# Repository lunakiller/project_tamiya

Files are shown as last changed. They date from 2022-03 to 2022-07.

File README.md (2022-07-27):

# Project TAMIYA

GitHub repository for custom open-source RC car system based on STM32 microcontrollers. The project is built on top of an old Tamiya QD chassis, which was modified. The repository includes both car and transmitter software along with hardware schematics and the Bachelor's thesis with extensive description of the project.

## Features

- long range (350 m+)
- high speed (35 km/h)
- smooth control (~220 Hz control loop)
- 2.4 GHz two-way communication 
- available driving data:
	- battery voltage and current
	- BLDC shell temperature
	- linear acceleration and angular velocity
	- supports logging to microSD card

## Car

- STM32F303CCT6 MCU
- nRF24L01+ PA + LNA module
- RC servo Emax ES3001
- GoolRC 2435 BLDC 4800Kv with 25A ESC
- OLED display and RGB LED
- ACS712 hall current sensor
- DS18B20 temperature sensor
- MPU6050 IMU

## Transmitter

- STM32F303CCT6 MCU
- nRF24L01+ PA + LNA module
- OLED display and RGB LED
- Custom PCB

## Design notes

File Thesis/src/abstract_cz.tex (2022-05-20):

\section*{Abstrakt}
\vspace{0.5cm}

Tato práce se zaměřuje na vývoj auta na dálkové ovládání poháněného STM32 mikrokontroléry. Popisuje stavbu jak auta, tak i vysílačky, představuje použité hardwarové části a jejich využití a~podrobně vysvětluje řídicí software.

Řídicí systém byl od základu vyvinut na starém podvozku Tamiya a tvoří ho na míru vyrobená ovládací deska s moduly a nezbytný řídicí software. Podvozek byl upraven a vybaven výkonnějším BLDC motorem. Aby bylo možné modernizovat vysílačku, byla navržená vlastní deska plošných spojů. Kromě základních funkcí je vůz vybaven různými senzory a moduly s~možností záznamu dat na micro SD kartu. Stav vozu je také nahlašován zpět do vysílačky a~zobrazován na OLED displeji.

Vyvinutý RC systém je v závěru práce otestován v reálných podmínkách. Kromě toho je změřen maximální kontrolovatelný dosah a maximální rychlost.

\vspace{1cm}
\noindent{\bf Klíčová slova:} STM32, RC auto, řídicí software, vestavěný systém, retrofitting

\noindent{\bf Překlad názvu:} Vývoj RC auta řízeného pomocí STM32 mikrokontrolerů

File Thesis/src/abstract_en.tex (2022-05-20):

\section*{Abstract}
\vspace{0.5cm}

This thesis focuses on the development of a radio-controlled car powered by STM32 microcontrollers. It describes the building of both the car and transmitter, presents hardware parts and~their utilization, and explains the control software in detail.

The controlling system was developed from scratch on top of an old Tamiya chassis and consists of a custom-made control board with modules and necessary control software. The~chassis was modified and equipped with more powerful BLDC motor. In order to retrofit the transmitter, a custom PCB was designed. In addition to the essential functions, the car features various sensors and modules with the ability to log the data to the micro SD card. Also, the car status is reported back to the transmitter and visualized on an OLED display.

The developed RC system is tested in real conditions at the end of the thesis. Besides, the~maximum controllable range and top speed are measured.

\vspace{1cm}
\noindent{\bf Keywords:} STM32, RC car, control software, embedded system, retrofitting

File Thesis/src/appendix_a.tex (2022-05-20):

\includepdf[pages=1, angle=90, scale=0.78, offset=0 -45, pagecommand=\appendix{Schematics}]{fig/ProjectTamiya_Car_schematics.pdf}
\newpage
\includepdf[pages=1, angle=90, scale=0.78, offset=0 -20, pagecommand={}]{fig/ProjectTamiya_TX_schematics.pdf}

\newpage
\appendix{Supplementary material}
The attached DVD shares the same file structure as mentioned GitHub repository and is described below. Only the folders have been compressed into zip archives.

\begin{table}[h]
   \renewcommand{\arraystretch}{1.1}
   \centering
%    \caption{ARM Core utilization in STM32 family}
    \label{tab:abbrev}   
    \begin{tabular}{c c}
       \noalign{\hrule height 1.1pt}\noalign{\smallskip}
	   \bfseries File & \bfseries Contents\\[0.2em]
	\noalign{\hrule height 1.1pt}\noalign{\smallskip}  

Software.zip 			& source codes and drivers for both control applications, shared libraries \\
Hardware.zip 			& KiCad schematics and gerber files \\
3D\_printed\_parts.zip	& STL models for 3D printing \\
Logs.zip					& Two example logs in CSV format \\

       \noalign{\smallskip}\noalign{\hrule height 1.1pt}
    \end{tabular}
\end{table}

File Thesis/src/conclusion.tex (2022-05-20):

%!TEX ROOT=main.tex

\part{Conclusion}
\label{chap:conclusion}
The thesis aimed to utilize the STM32 microcontrollers to develop and control an RC car. STM32 families of microcontrollers were summarized, and their architecture and the most commonly used peripherals were briefly described.

The whole system was developed from scratch, aside from the chassis and other plastic parts. It utilizes readily available parts, including an RC servo and BLDC motor with the controller, sensor boards, and modules. These functional blocks were introduced, and their purpose and actual use were explained. Since it is an RC car, meaning 'Radio Controlled', the control transmitter was developed as well.

A custom control board was designed for both platforms. The car's control board is made on a perfboard and consists primarily of modules and connectors. This approach is simple, quick, flexible, and certainly sufficient for the use case. However, space constraints inside the transmitter asked for a custom PCB design that would provide better space utilization. Therefore, the circuit board was designed according to the original, slightly modified to fulfill current needs, and manufactured.

The resulting RC system was to be unconventional in terms of available features. Accordingly, both the transmitter and the car received an OLED display and RGB LED to report the status. In addition, the car is equipped with various sensors. A micro SD card slot is available to record all the data.

After the hardware design, a control software had to be developed. As the software controls real devices in real time, it is primarily interrupt-driven and implemented with an emphasis on speed to guarantee periodic execution of the control loop and thus smooth control of the car. Nevertheless, it is also designed to be user-friendly and encompasses interactive battery voltage and signal strength indicators that should simplify navigation on display along with other icons.

At the end of the thesis, the RC system is tested in real conditions with successful results. Besides the essential RC car functions, all the unconventional functions also proved to work. The control is responsive. The car's top speed is 35km/h, and the maximum controllable range is 375m.

All the schematics, source code, and 3D models are available at a GitHub repository\footnote{\url{https://github.com/lunakiller/project_tamiya}} and on the attached DVD.

Even though the feature is not implemented in the project's current state, microcontroller pins PA11 and PA12 on the car's control board are reserved for the USB peripheral. Therefore, a single-board computer like RaspberryPi running a control software can possibly control the car through the USB, and the chassis can, for example, become a platform for testing autonomy.

The future work can possibly be replacing the commercial ESC controlling the motor with some custom-made solution that would offer a more advanced motor control algorithm. This upgrade would increase the top speed, prolong battery life, and provide the user with more driving data.

Another future step would be replacing the present 6-axis IMU with a 9-axis IMU with an incorporated magnetometer to obtain the precise position in space and utilize those data for control or mapping purposes. One possibility would be to utilize those data to implement 'stability control' to help steer the car in a skid or at high speeds, where the car is tricky to control.

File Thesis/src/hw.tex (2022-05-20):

%!TEX ROOT=main.tex

\part{Hardware}
\label{chap:hw}
%\section{Indroduction}
%\label{sec:hw_intro}

\section{Chassis and transmitter}
\label{sec:hw_base}
\subsection{Background}
The whole project is built on an old entry-level onroad 1/10 chassis from the \textit{Tamiya Quick Drive} series released on Jul 16, 2003 \cite{tamiya}. The RC car was obtained as a childhood gift. It was pre-assembled and came with a 2-channel transmitter communicating at a frequency of \SI{27}{\MHz}. Later the servo broke, and no repair or upgrade parts were available. Since the repair was nearly impossible, but the rest of the chassis was fully functional, it was the perfect choice for a complete rebuild.

The car featured a sealed gearbox, servo, '280' size brushed motor and \SI{9.6}{\V} Ni-Cd battery pack. Due to the age of the product, not much technical information can be found. Figure \ref{fig:tx_old_pcb} shows the old transmitter PCB.
\begin{figure}[ht]
\centering

\caption{Original transmitter PCB}
\label{fig:tx_old_pcb}
\end{figure}

\subsection{Modifications}
\label{sub:hw_mods}
All the electronics were removed, leaving only the plastic chassis. The broken 5-wire servo was replaced with a 'standard' size hobby servo used in most 1/10 RC cars. The old brushed motor was still functional, but it was decided to replace it with a newer and more powerful one. The only constraint was a shaft size, as the old pinion had to be transferred to the new motor to maintain functionality. Therefore a '2435' size BLDC motor with a \SI{25}{\A} ESC (Electronic Speed Controller) was selected. More information about the servo and BLDC is in sections \ref{sec:hw_servo} and \ref{sec:hw_bldc}. Furthermore, the plastic bearings were replaced by metal ball bearings.

A 2-cell LiPo battery with a capacity of \SI{2200}{\milli\A\hour} was chosen to supply power to the electronics. According to the product specification, this battery should withstand 35C of continuous current~\cite{lipo_car}. The term '35C' means '35 times the battery capacity'. For this particular battery, that means ${35 \cdot \SI{2.2}{\A} = \SI{77}{\A}}$ of current, which is more than sufficient.

The transmitter underwent a similar procedure. The original circuit board and the antenna were also removed, retaining only trigger potentiometers and plastic parts. Potentiometers used for throttle and steering trimming were replaced with rotary encoders. Again, the power supply is a 2-cell LiPo battery with a lower capacity of only \SI{900}{\milli\A\hour} and 25C of continuous current \cite{lipo_tx}.

\section{Servo}
\label{sec:hw_servo}
A servomotor, or servo for short, is an actuator used for precise output shaft positioning. It consists of a motor with position feedback and a control board. RC servos are controlled using a 50Hz PWM signal. The output angle is linearly dependent on a pulse width between \SI{1}{\ms} and \SI{2}{\ms}. The diagram in figure \ref{fig:servo_control} illustrates typical timing.
\begin{figure}[ht]
\centering

\caption{Servomotor timing diagram \cite{servo_control}}
\label{fig:servo_control}
\end{figure}

The servo used in the car is \textit{EMAX} ES3001. It has plastic gears and operating voltage between \SI{4.8}{\V} to \SI{6.0}{\V}. Speed and torque depend on the supply voltage. According to the product specifications \cite{emax}, the servo can achieve an operating speed of $0.17\, \text{s}/60^\circ$ and torque of \SI[inter-unit-product =\ensuremath{\cdot}]{3.2}{\kg\cm} with the \SI{4.8}{\V} supply voltage. From the operating speed we can calculate angular velocity: 
\begin{equation}
\omega = \frac{d \theta}{d t} = \frac{\frac{\pi}{3}}{0.17} \doteq 6.156\ \unit{\radian\per\second}\ ,
\end{equation}
where $\frac{\pi}{3}$ is $60^\circ$ converted to radians.
Since the servo supply voltage is \SI{5}{\V}, both speed and torque values should be slightly higher.

\section{Motor and ESC}
\label{sec:hw_bldc}
As mentioned in section \ref{sub:hw_mods}, the biggest BLDC with a shaft diameter of \SI{2}{\mm} was selected to replace the old brushed one. The motor was supplied in a set including a \SI{25}{\A} ESC. The type is \textit{GoolRC} 2435 \SI{4800}{\Kv}\footnote{\unit{Kv} refers to rpm/V with no load attached to the motor shaft.} BLDC; available information about the motor is in table \ref{tab:BLDC_spec} and about ESC in table \ref{tab:ESC_spec}.
\begin{table}[h]
   %\renewcommand{\arraystretch}{1.1}
   \tabcolsep 18pt
   \centering
    \caption{BLDC specifications}\label{tab:BLDC_spec}   
    \begin{tabular}{l r}
       \noalign{\hrule height 1.1pt}\noalign{\smallskip}	   
	Power			& 300\unit{\W}\\
	Max. voltage   	& 12.6\unit{\V}\\
	Max. current   	& 24\unit{\A}\\
	Rotor poles	   	& 4 \\
	\unit{\Kv} rating	  	& 4800 \\
	Length			& 24\unit{\mm} \\
	Diameter			& 35\unit{\mm} \\
	Shaft diameter	& 2\unit{\mm} \\
       \noalign{\smallskip}\noalign{\hrule height 1.1pt}
    \end{tabular}
\end{table} 
\begin{table}[h]
   %\renewcommand{\arraystretch}{1.1}
   \tabcolsep 12pt
   \centering
    \caption{ESC specifications}\label{tab:ESC_spec} 
    \begin{tabular}{l r}
       \noalign{\hrule height 1.1pt}\noalign{\smallskip}
	Continuous current		& 25\unit{\A}\\
	Instantaneous current   	& 50\unit{\A}\\
	BEC type				   	& 5\unit{\V}, 2\unit{\A}\\
	Battery				   	& 2-3 Cell LiPo \\
       \noalign{\smallskip}\noalign{\hrule height 1.1pt}
    \end{tabular}
\end{table} 

Originally the brass pinion was press-fitted to the motor; however, the shaft began to slip inside the pinion. Therefore it was soldered to the shaft with the help of solder paste and a hot-air station.

Since the BLDC motor is directly connected to the ESC and the control board communicates only with the ESC, the BLDC is considered a black box.

RC ESCs are controlled the same way as RC servos; thus, the same timing diagram in figure \ref{fig:servo_control} applies. The only difference is the resulting motion. Pulse width with a duration of \SI{2}{\ms} equals full forward acceleration, pulse width with a duration of \SI{1.5}{\ms} equals neutral, and pulse width with a~duration of \SI{1}{\ms} equals full brake/reverse.

Whether the brake or reverse is activated depends on the actual motion of the motor. If the car is going forward (meaning the motor rotates forward) and the pulse width becomes lower than \SI{1.5}{\ms}, first, the brake is activated. The car must be almost static to start reversing; otherwise, the ESC will stay in brake mode. If the car is static or is already reversing, a pulse width lower than \SI{1.5}{\ms} activates reverse mode.

\section{Control board}
\label{sec:hw_control}
Prototyping was mainly done on the breadboard using the \textit{RobotDyn's} BlackPill development board featuring STM32F303CCT6 microcontroller \cite{black_pill}. The board uses a similar size and form factor as the popular BluePill board equipped with STM32F103C8T6 \cite{blue_pill}. Both these boards were readily available.
    \begin{figure}[h]
    \centering
    \begin{subfigure}{0.4\textwidth}
    \centering
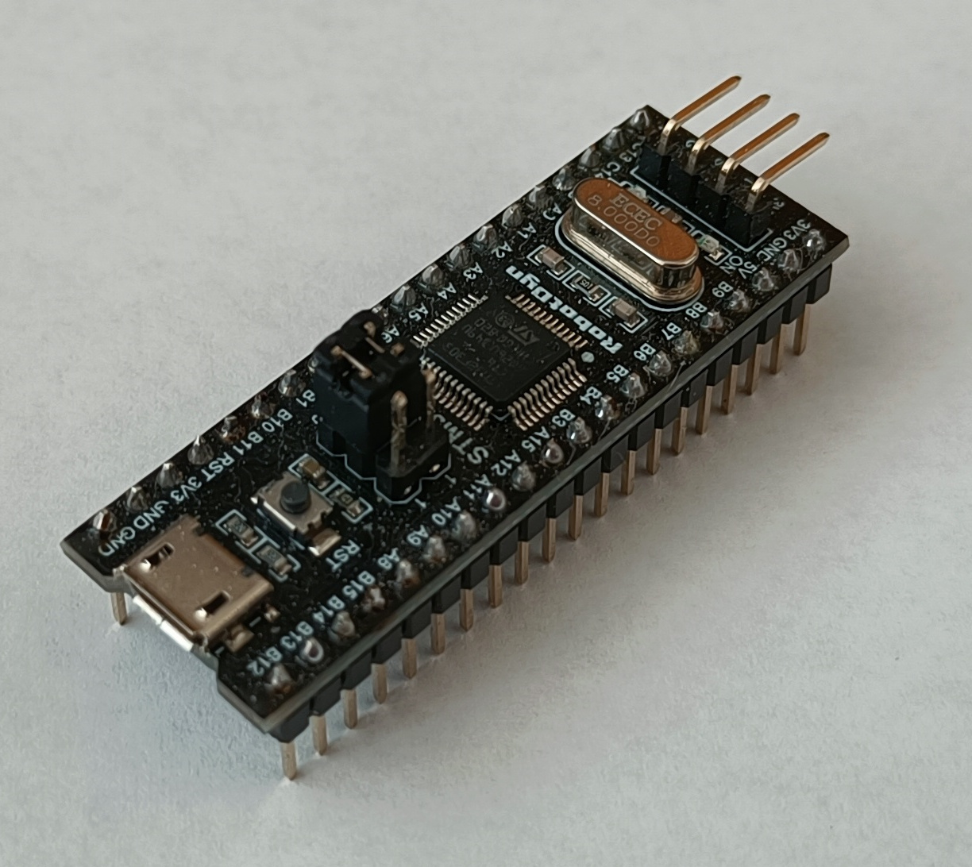
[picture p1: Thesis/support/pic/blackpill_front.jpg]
        
		\caption{front side}
    \end{subfigure}%
    \hspace{1cm}
    \begin{subfigure}{0.4\textwidth}
    \centering
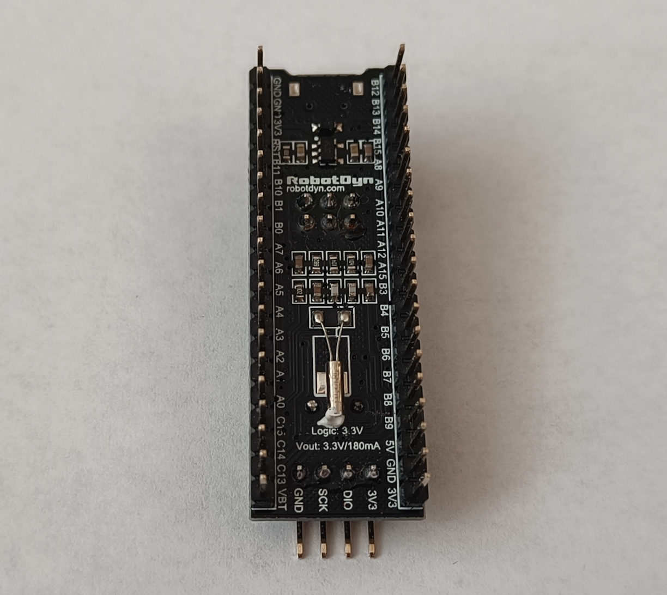
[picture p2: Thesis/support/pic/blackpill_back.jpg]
		
		\caption{back side}
    \end{subfigure}
	\caption{RobotDyn BlackPill development board}
    \label{fig:black_pill}
    \end{figure}

BlackPill was selected for its better processor based on an ARM M4 core with FPU, larger memories, and more advanced peripherals. Thus, it is more suitable for processing data from more sensors, especially when using floating point arithmetics. The board is shown in figure \ref{fig:black_pill}.

%\begin{figure}[t]
%\centering
%\includegraphics[width=0.5\linewidth]{fig/placeholder.jpg}
%\caption{*PLACEHOLDER* RobotDyn BlackPill development board}
%
%\end{figure}

\section{Communication}
\label{sec:hw_comm}
The project uses wireless modules equipped with nRF24L01+ transceiver chip from \textit{Nordic Semiconductor}, a power amplifier, a low-noise amplifier, and an external antenna. The chip operates in the worldwide \SI{2.4}{\GHz} ISM band and communicates with the MCU using the SPI bus. Configurable parameters include channel, data rate, and output power. These modules fit all the requirements, and in addition, they are cheap and readily available.

According to the product specification \cite{nrf_pa_lna}, the range should be more than \SI{800}{\m} line-of-sight. Thanks to the \textit{Enhanced ShockBurst protocol} and its Auto Acknowledgement function \cite{nrf_datasheet}, attaching a small payload to the ACK packet is possible. This feature is advantageously used to report car status back to the transmitter.
\begin{figure}[h]
\centering
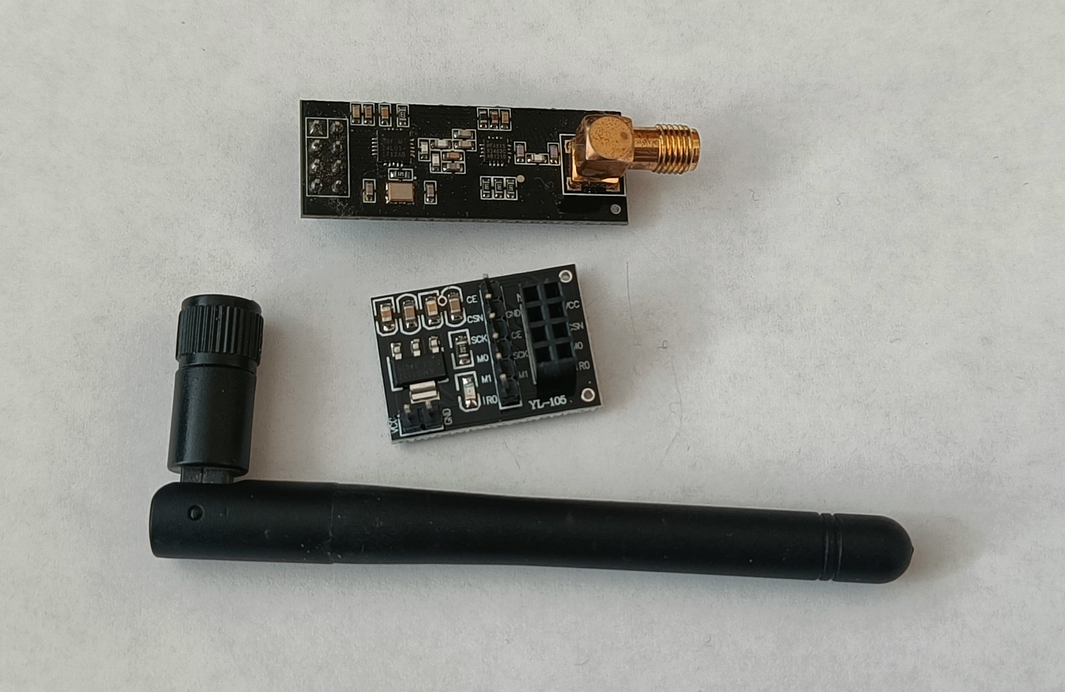
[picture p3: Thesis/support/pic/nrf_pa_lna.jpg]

\caption{Unmodified nRF24 module with adapter}
\label{fig:unmod_nrf}
\end{figure}

An additional adapter board is utilized to supply voltage to the nRF24 module. It has the same pinout and includes a voltage regulator with all needed external components. The Adapter board is powered with \SI{5}{\V}, which are then regulated to \SI{3.3}{\V}. This setup ensures a stable power supply for the nRF24 module.

As the adapter board is only equipped with a pin socket for connection, which is unsuitable for use in vibration generating environments, it was removed. The nRF24 module was instead soldered directly to the adapter, as were the wires. The entire communication module is thus more robust and takes up less space. Figure \ref{fig:unmod_nrf} shows the unmodified communication module with the adapter board.

\section{Sensors}
\label{hw_sensors}
In addition to measuring the voltage, which is necessary for battery monitoring and is realized using a voltage divider, the car also measures current and BLDC case temperature. It is also equipped with 6-axis IMU. In the project's present state, data from sensors are mainly informative and are not used for control purposes.

The transmitter does not use any particular sensor; only battery voltage is measured via the voltage divider.

\subsection{Current}	
The current is measured using a module with a \SI{30}{\A} version of an ACS712 chip from \textit{Allegro MicroSystems}. It is a small linear current sensor based on the Hall effect. Current flowing through the sensor's copper terminals generates a magnetic field, which is then sensed by the integrated Hall-effect circuit. The sensor module is in figure \ref{fig:acs712}.
\begin{figure}[h]
\centering
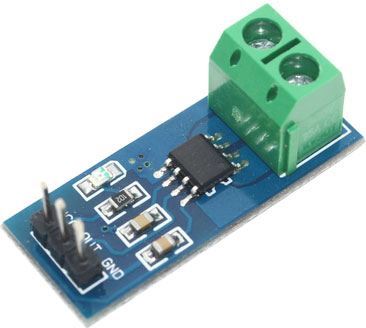
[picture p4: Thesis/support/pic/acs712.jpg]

\caption{ACS712 current sensor \cite{acs_pic}}
\label{fig:acs712}
\end{figure}

The output of the sensor is a voltage proportional to the flowing current. If no current is flowing, the sensor output is the supply voltage divided by two. If a positive current flows, the output voltage increases, whereas the output voltage decreases if the current is negative.

Current sense terminals are electrically isolated from the rest of the sensor; therefore, it is possible to measure high voltages without external electrical isolation. The sensor is capable of measuring both AC and DC current with a stated total output error of $1.5\%$ \cite{acs_datasheet}.

\subsection{Temperature}
A digital thermometer DS18B20 provides temperature measurement. The sensor is manufactured by \textit{Dallas Semiconductor}, which \textit{Maxim Integrated} later acquired. It can measure temperatures from \SI{-55}{\degreeCelsius} to \SI{125}{\degreeCelsius}. It has a programmable resolution ranging from 9 to 12 bit and $\pm$\SI{0.5}{\degreeCelsius} accuracy over most of the measuring range. The sensor uses a 1-Wire interface, which requires only one pin for communication. When combined with parasitic power mode, the whole thermometer requires only two pins for operation \cite{ds_datasheet}.

The project uses the TO-92 package, which was advantageous because of the limited space around the BLDC. The small size made it possible to mount the sensor on the back of the motor housing with the aid of heat-conducting foil. The sensor is in figure \ref{fig:ds18b20}.
\begin{figure}[h]
\centering
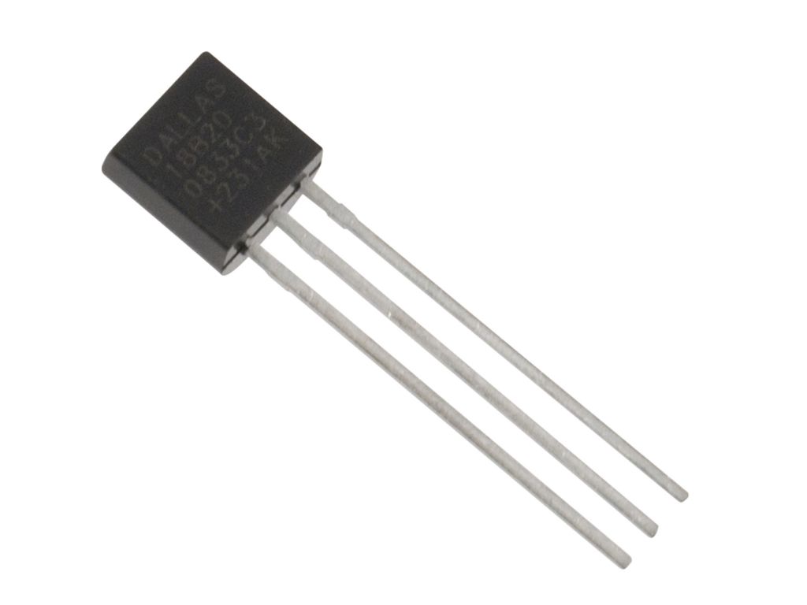
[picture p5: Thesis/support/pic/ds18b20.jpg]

\caption{DS18B20 temperature sensor \cite{ds_pic}}
\label{fig:ds18b20}
\end{figure}

\subsection{IMU}	
For motion measurements, a module with MPU6050 from \textit{InvenSense} was selected. The module is in figure \ref{fig:mpu}. The sensor packs a 3-axis accelerometer, which provides linear acceleration data, and a 3-axis gyroscope, which provides angular velocity data, in one chip. Both the accelerometer and gyroscope have programmable measurement ranges. Communication with the sensor is performed using the I\textsuperscript{2}C bus. An external 3-axis magnetometer can be attached straight to the sensor, extending the sensor's capability \cite{mpu_datasheet}.
\begin{figure}[h]
\centering
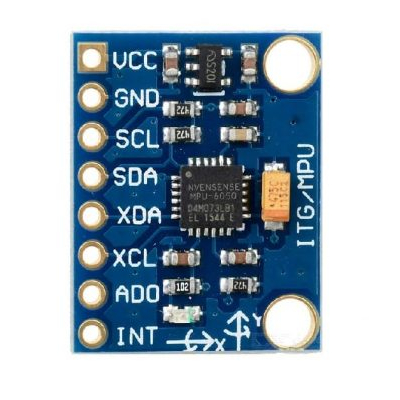
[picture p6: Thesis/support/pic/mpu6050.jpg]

\caption{MPU6050 IMU module \cite{mpu_pic}}
\label{fig:mpu}
\end{figure}

The sensor claims it has a DMP (Digital Motion Processor) capable of merging the accelerometer and gyroscope data on-chip. Sadly, this feature is undocumented and available only when using \textit{InvenSense's} official \textit{Embedded MotionApps software}. Another possibility would be using \textit{I\textsuperscript{2}Cdevlib}, where the DMP functionality was reverse-engineered \cite{i2cdevlib}. However, the \textit{I\textsuperscript{2}Cdevlib} is written for Arduino and would require porting the code to the STM32 with uncertain results. Therefore only raw accelerometer and gyroscope data are used.

\section{Status info}
\label{sec:hw_status}
Neither the RC car nor the transmitter reported any status in the original version. The user had to check the battery state himself; otherwise, the battery could be discharged entirely and damaged. Since LiPo batteries should not be discharged below a certain threshold, the usual rule of thumb across the RC community is not to discharge the battery below \SI{3.1}{\V} per cell, it was necessary to report the battery status.

An RGB LED was chosen for that purpose because it is possible to quickly report the various states to the user using different colors. On the other hand, it is unsuitable for visualizing values such as temperature. Besides, the transmitter has its own battery, whose status should also be reported to the user, and that would need 2 LEDs. The single RGB LED was therefore insufficient for the transmitter.

For this reason, the display seemed like a good alternative and replacement. An OLED display was convenient as its power consumption is low, it is readable in direct sunlight, and thanks to only one color, it is fast. The disadvantage is its small size, which complicates the orientation in the displayed data.

Considering all the factors, both the RGB LED and the OLED display were used. RGB LED serves as a fast state notifier, and further status information can be found on the display.

Both car and transmitter use RGB LED with a common anode and monochrome OLED display module with SSD1306 chip communicating using I\textsuperscript{2}C bus. %TODO citace?

%\begin{table}[t]
%\centering
%\caption{*PLACEHOLDER* BLDC specifications} %TODO citace
%\includegraphics[width=0.8\linewidth]{support/pic/placeholder.jpg}
%\label{tab:BLDC_spec}
%\end{table}

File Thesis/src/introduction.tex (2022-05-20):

%!TEX ROOT=main.tex
\begin{figure}[ht]
\centering
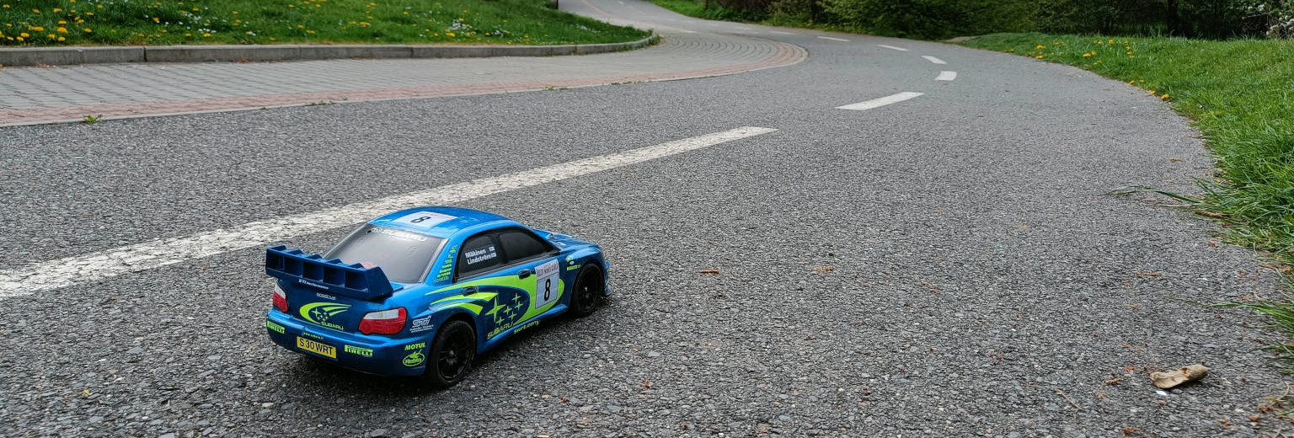
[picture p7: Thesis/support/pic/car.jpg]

%\caption{Used chassis}
\end{figure}
\part{Introduction}
\label{chap:intro}
\begin{myparindent}{20pt}
This thesis focuses on utilizing STM32 microcontrollers to design and build an RC car control board. As the project is Radio Controlled, a control device - a transmitter - had to be developed as~well. Both devices are constructed primarily from available modules, which were sometimes modified and combined to form a working RC system.
\end{myparindent}

Therefore, the thesis contains the development of both devices and describes the functional blocks used. The necessary control software, which was developed for both devices, is also presented and explained in detail. Finally, the designed system was tested in real conditions.

The proposed car control system is retrofitted to a particular chassis, but the application of a standard RC control signal using PWM makes it possible to mount the control board to a different chassis with a different servo and motor.

\section{Motivation}
The main motivation was to build an RC car with an STM32 microcontroller that would function and behave like a regular RC car, but at the same time, would be extraordinary. Extraordinary, for example, in terms of range, non-standard features, or user customizability.

Most commercially available RC systems are proprietary and closed and use undocumented components, thus making the modification hard or even impossible. Some hardware modifications are possible with expensive accessories, but the control software customization is usually impossible even with the accessories. This prohibits, for example, advanced driving data reporting and recording or~the~use of custom sensors.

The solution proposed in this thesis solves the problem, as control boards are built from available and community-known modules, and the control software written in C language is open-source. Additionally, the car control board contains various sensors and a micro SD card slot to record driving data, which can be later visualized and analyzed.

Since the project is not built from scratch and as a base uses an old chassis and transmitter with no spare parts available, another motivation was to make all the modifications with minimal physical intervention to reduce the risk of irreversibly breaking it.

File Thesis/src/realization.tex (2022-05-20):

%!TEX ROOT=main.tex

\part{Realization}
\label{chap:realization}
Since there are no spare parts available for the transmitter or the car, all modifications have been made with as little structural intervention as possible. This process can be referred to as retrofitting.

\section{Transmitter}
\label{sec:real_tx}
\subsection{Power supply}
As described in section \ref{sub:hw_mods}, the transmitter is powered by a 2-cell LiPo battery with a nominal voltage of \SI{7.4}{\V}. The battery is connected via an XT60 connector and a switch to a step-down converter module with an LM2596 chip. The module is needed to regulate the battery voltage to \SI{5}{\V} to power the control board.

This voltage is used for the RGB LED, communication module, and linear voltage regulator AP2111, which regulates it to \SI{3.3}{\V} used to power the rest of the components. This regulator was selected because of the low dropout voltage of only \SI{250}{\mV} and high output current of \SI{600}{\mA} \cite{ap_datasheet}.

In order to measure the battery voltage with the processor's internal ADC, it first had to be lowered to fit within the ADC range, which is \SIrange{0}{3.3}{\V}. Therefore a voltage divider is soldered to the input terminals of the step-down module. The divider was designed to use resistors with standard values and is pictured in figure \ref{fig:tx_div}. The resistor values are R1 = \SI{22}{\kohm}, R2 = \SI{10}{\kohm}.
\begin{figure}[h]
\centering

\caption{Voltage divider utilized in transmitter }
\label{fig:tx_div}
\end{figure}

A fully charged 2-cell LiPo battery reaches \SI{8.4}{\V}, then the output of the divider equals
\begin{equation}
	U_{adc} = U_{batt} \cdot \frac{R2}{R1+R2} = \SI{2.625}{\V}\ ,
\end{equation}
which is safely within the ADC range.

\subsection{Controls}
The transmitter was supplied with a steering wheel and throttle trigger as \SI{5}{\kohm} potentiometers. Since they are old, a \SI{100}{\nF} capacitor was added between the output pin of both potentiometers and ground to form a low-pass filter and smooth out the output signal.

Potentiometers used for control trimming were replaced with quadrature rotary encoders with push-buttons. Encoders have screw threads, which fit into the original holes. Since encoders are fixed to the transmitter, a simple connector made from a pin socket was soldered to encoder pins.

\subsection{PCB design}
    \begin{figure}[b]
    \centering
    \begin{subfigure}{0.495\textwidth}
    \centering
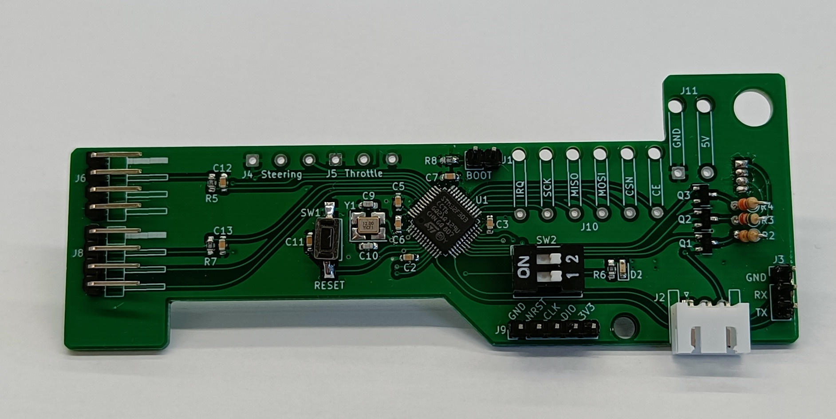
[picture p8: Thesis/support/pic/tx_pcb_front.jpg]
        
		\caption{front side}
    \end{subfigure}%
    \hfill
    \begin{subfigure}{0.495\textwidth}
    \centering
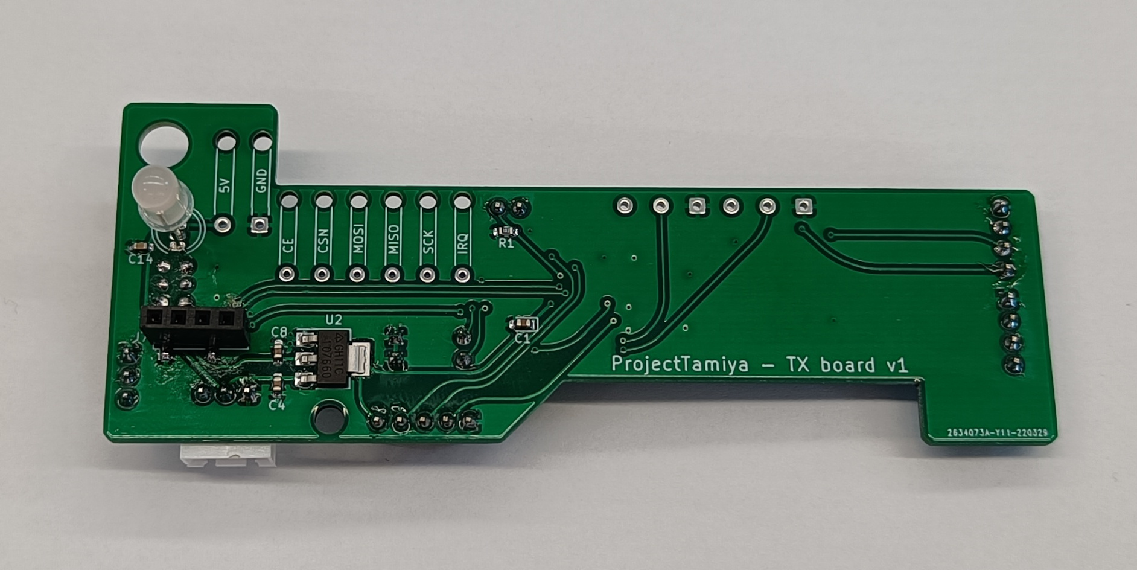
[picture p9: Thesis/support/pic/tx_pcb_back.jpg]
		
		\caption{back side}
    \end{subfigure}
	\caption{PCB for transmitter}
    \label{fig:tx_pcb}
    \end{figure}

As the space in the transmitter case was limited, it was decided not to use the perfboard but to create the PCB. It was designed in KiCad and manufactured by JLCPCB. The board consists of connectors, a voltage regulator, an MCU circuit with a crystal oscillator, and an RGB LED driven by N-channel MOSFETs. All traces are rounded to eliminate the possibility of signal reflection. Figure \ref{fig:tx_pcb} shows the PCB before final soldering to the transmitter, and figure \ref{fig:tx_assembly} shows the assembled transmitter.

As stated in section \ref{sec:hw_control}, the prototyping was done using a BlackPill board with a microcontroller STM32F303CCT6. This microcontroller was suitable and was therefore selected also for the final design.

First, the original PCB was measured so that the new PCB could be designed according to these dimensions. A minor modification was done; the new PCB has a cutout on the top to fit the nRF24 communication module.

The communication module and control potentiometers are directly soldered to the board. In contrast, the power supply is connected via the JST XH connector, and rotary encoders are connected via simple pin sockets visible on the left side in figure \ref{fig:tx_assembly_a}.
\begin{figure}[h]
    \centering
    \begin{subfigure}{0.4\textwidth}
    \centering
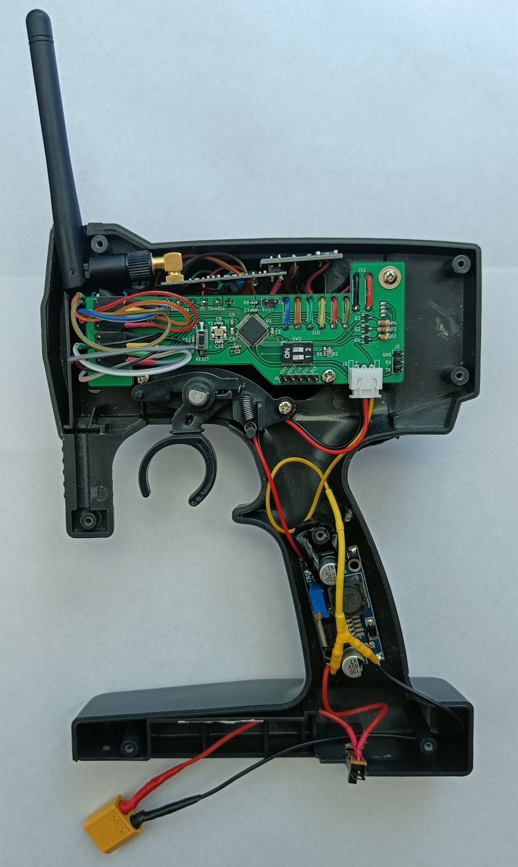
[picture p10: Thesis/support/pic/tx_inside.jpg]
        
		\caption{inside view}
		\label{fig:tx_assembly_a}
    \end{subfigure}%
    \hspace{1cm}
    \begin{subfigure}{0.4\textwidth}
    \centering
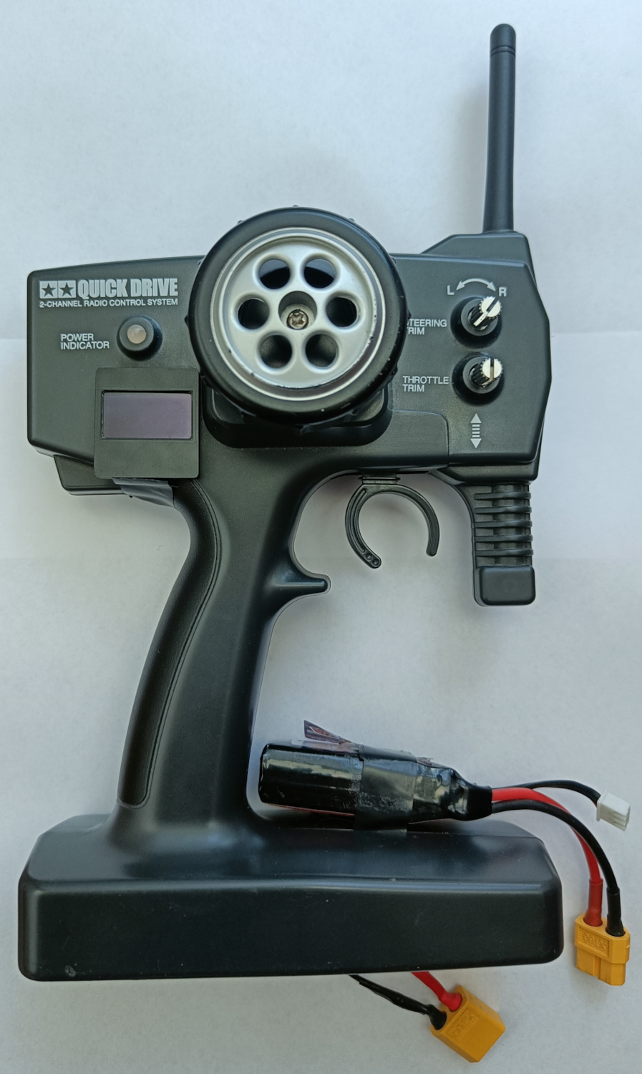
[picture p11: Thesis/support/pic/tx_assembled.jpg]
		
		\caption{front side}
    \end{subfigure}
	\caption{Assembled transmitter}
    \label{fig:tx_assembly}
    \end{figure}

Microcontroller circuitry was designed according to Section 7 of \cite{f3_design_an}. Four \SI{100}{\nF} ceramic decoupling capacitors were placed as close to the microcontroller as possible. Since the VBAT pin is not utilized, it was connected to the supply voltage (VDD) via another \SI{100}{\nF} ceramic capacitor. A bigger \SI{4.7}{\uF} decoupling capacitor is placed on the main supply line close to the microcontroller.

The reset circuit was also inspired by \cite{f3_design_an} and consists of a button and a capacitor connected to reduce the push-button bouncing effect. BOOT0 pin is pulled to the ground with a resistor, but switching the boot mode with a jumper placed on J1 is possible.

External \SI{12}{\MHz} crystal oscillator XT324 with a load capacitance of \SI{20}{\pF} provides the clock for the microcontroller \cite{xt324_datasheet}. The circuit of the oscillator is in figure \ref{fig:osc}. Equation \ref{eq:load_cap} mentioned in Section 3.3 of \cite{osc_design_an} was used to calculate values of external load capacitances:
\begin{equation}
C_L = \frac{C_{L1} \cdot C_{L2}}{C_{L1} + C_{L2}} + C_S\ ,
\label{eq:load_cap}
\end{equation}
where $C_L$ is the crystal's desired load capacitance, $C_{L1}$ and $C_{L2}$ are values of external capacitors and $C_S$ is the stray capacitance of the printed circuit board and connections. A rough estimate of $C_S = \SI{7}{\pF}$ according to Section 6.3.7 of \cite{f303_datasheet} and Section 3.3 of \cite{osc_design_an} was used for computation. Assuming that $C_{L1} = C_{L2}$, we have
\begin{equation}
C_L - C_S = \frac{C_{L1} \cdot C_{L1}}{C_{L1} + C_{L1}} = \frac{C_{L1}}{2} = \SI{13}{\pF}\ ,
\end{equation}
and therefore the external load capacitance should be \SI{26}{\pF}. As this is a non-standard value, \SI{27}{\pF} capacitors were used instead.
\begin{figure}[h]
\centering

\caption{Crystal oscillator circuit}
\label{fig:osc}
\end{figure}

The RGB LED resistor values were chosen experimentally to achieve similar luminosity of all channels as no datasheet is available. If all channels are active, the total current through the LED does not exceed the assumed maximal \SI{20}{\mA}.

\section{Car}
\label{sec:real_car}
\subsection{Power supply}
The main power source is a 2-cell LiPo battery discussed earlier in section \ref{sub:hw_mods}, which is connected via an XT60 connector to the ESC.

Between the battery and ESC is an ACS712 current measurement module with XT60 connectors on both sides. The module is connected backward as only a positive current is measured. Consequently, the sensor output is within 0.5 to 2.5V, and ADC can safely measure it without extra components.

The control board is powered by ESC's Battery Elimination Circuit (BEC), producing \SI{5}{\V} with a~maximum current of \SI{2}{\A}. Therefore ESC's power switch also acts as the main power switch. Moreover, BEC supplies power to the servo, current sensor, and, as with the transmitter, to the communication module and LEDs.

The rest of the electronics is powered by \SI{3.3}{\V} regulated by BlackPill's onboard voltage regulator. Marking on the bottom side of the board claims that the regulator can produce \SI{180}{\mA} of output current, which should be sufficient to power all the components; hence no external voltage regulator was added.

\subsection{Board design}
The Control board for the car was created on the perfboard as it allowed for more flexibility in design and testing, and the space available in the car is quite ample. The schematic was drawn in KiCad. The board looks more complex than the board in the transmitter due to the number of components and consists of necessary connectors, a BlackPill board, an OLED display, an SD card slot, and LEDs.

The main BlackPill board is soldered directly to the perfboard to ensure rigidity. The OLED display and SD card slot were also soldered directly to the board under the BlackPill. Right under the display is a push-button used to wake it up. The UART debug pins are at the bottom left of the display, and to the right is a two-position DIP switch.

Everything not soldered to the board is connected using JST XH connectors. At first, simple pin headers were used as connectors, but the cable was sometimes disconnected from the board since the car moves and generates vibrations. JST XH connectors feature a small locking mechanism to reduce the risk of disconnection and are therefore suitable.

The board was designed so that connectors are grouped by type. In the upper left corner are the connectors for measuring the voltage, current, and temperature of the BLDC. More to the right are the connectors for the communication module, 2-pin for power, and 6-pin for SPI communication. To the right of the BlackPill board are connectors for controlling the car; closer to the board is the servo connector, and next to it is the ESC connector, which supplies voltage to the board. The last connector in the lower right corner is for the IMU. The picture of the board is in figure \ref{fig:car_pcb}.
\begin{figure}[t]
\centering
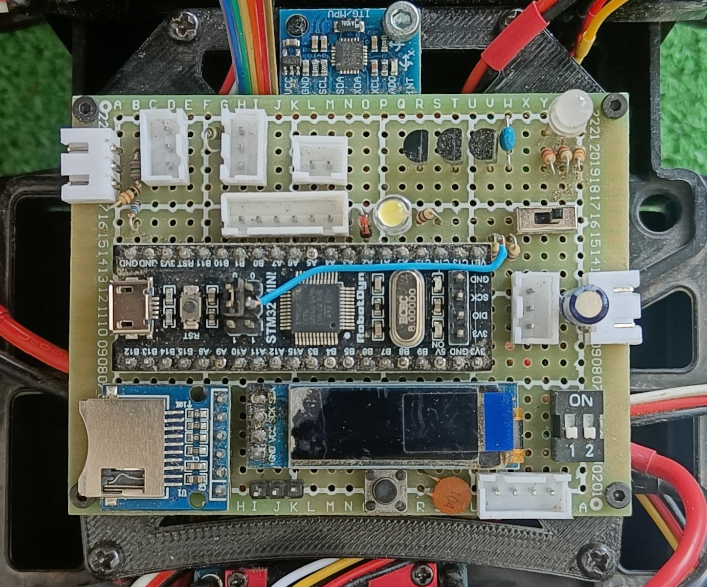
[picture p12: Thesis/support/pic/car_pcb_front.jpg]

\caption{Mounted perfboard for car}
\label{fig:car_pcb}
\end{figure}

In the right upper part of the board, there is again an RGB LED with individual channels driven by N-channel MOSFETs. The same resistor values were used since the RGB LED is the same type as the RGB LED in the transmitter. An additional wide-angle white LED controlled by a switch was mounted on the board. The purpose of this LED is to illuminate the car body, so the car is better visible at night.

As the BEC powers the control board with fixed \SI{5}{\V} output and there is no way to deduce the supply voltage without modifying the ESC, another method had to be found. LiPo batteries use the same JST XH connectors used on the control board to balance the cells when charging. Therefore, the~balance connector is advantageously used for battery monitoring. The user only needs to connect the battery balance connector to the appropriate socket on the board.

\subsection{Parts mounting}
The control board was fixed to the chassis simply with tape for the testing phase. As this is not ideal in the long term, it was decided to utilize the original mounting holes present in the chassis and design a frame that would fit into them to avoid drilling.

The frame design was made in \textit{Autodesk's} Fusion360 CAD software and manufactured on the 3D~printer. The frame is pretty simple; it serves as an 'adapter' for holes in the chassis and holes in the perfboard. The render is in figure \ref{fig:frame}. The control board mounting holes are \SI{5}{\mm} higher than the frame mounting holes to create a small gap.

There is also a mounting point for the IMU since it should be firmly attached to the chassis for correct measurements. Even though the IMU has two holes, it is mounted with only one screw. That is because the screw head in the second hole would interfere with electrical components on the IMU module.
\begin{figure}[h]
\centering
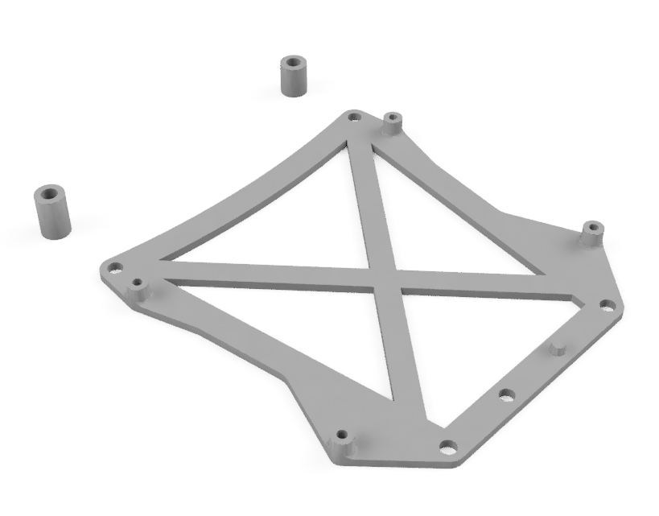
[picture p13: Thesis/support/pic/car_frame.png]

\caption{PCB frame}
\label{fig:frame}
\end{figure}

As the mounting holes in the chassis are not at the same height, custom spacers were also designed and 3D printed to level the whole frame. The assembled chassis with the frame is shown in figure \ref{fig:chasis}.
\begin{figure}[h]
\centering
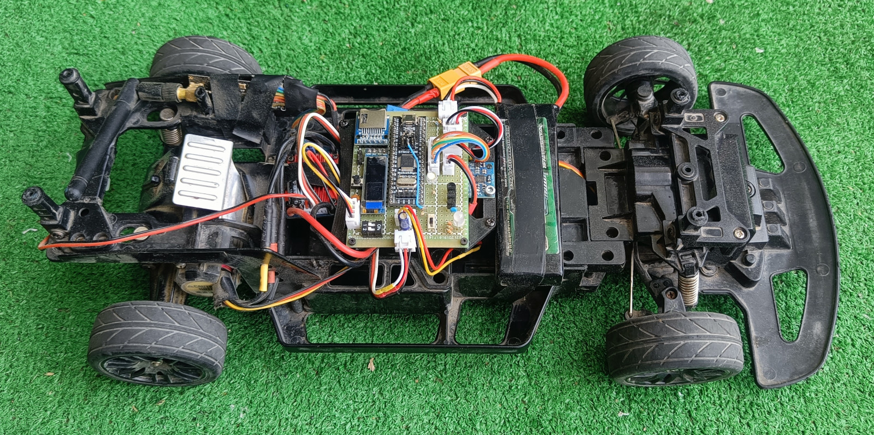
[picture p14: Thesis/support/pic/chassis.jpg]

\caption{Assembled chassis}
\label{fig:chasis}
\end{figure}

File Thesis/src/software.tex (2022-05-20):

%!TEX ROOT=main.tex

\part{Software}
\label{chap:software}
\section{Introduction}
The control program for both the transmitter and the car is written in C language. It utilizes the STM32 HAL (Hardware Abstraction Layer) libraries, and the STM32CubeMX graphical utility was used to set up the necessary initialization and project files and generate code for peripheral configuration. Afterward, the application is compiled using a Makefile under Linux by the GNU GCC cross-compiler for ARM bare-metal targets.

STM32 HAL driver library provides a set of APIs to simplify interaction with all the peripherals and thus the user application implementation. The HAL driver layer implements run-time failure detection to increase robustness. HAL APIs are available for all peripherals. Also, the API ensures high portability across different STM32 families \cite{hal}.

STM32CubeMX is a graphical tool that provides a convenient user interface to configure the microcontroller. It allows a simple configuration of pin assignments, peripherals, or the clock tree, and the corresponding C initialization code generation. It also packs middleware stacks, such as USB, FatFs, or TCP/IP. This tool notably speeds up the process of microcontroller configuration and allows the user to focus on the application \cite{cubemx}.

The control program is almost exclusively interrupt-driven. Emphasis has been placed on program execution speed to ensure a high frequency of control commands and thus smooth car control.

\section{File structure}
Software for both the transmitter and car is in their respective folders. STM32CubeMX generated the code, and to maintain compatibility, the dedicated user code sections were used. The code was generated with CubeMX's basic application structure setting.

Therefore, both project folders in the \textit{'Software'} folder contain the \textit{'Drivers'} folder with ARM and HAL drivers for the board, the \textit{'Inc'} folder with header files, and the \textit{'Src'} folder with source files. The startup file, makefile, linker script, and CubeMX project file are in the root folder. As the car implements FatFs driver, it is located mainly in the \textit{'Middlewares'} folder.

The \textit{'shared\_libs'} folder contains shared libraries for both applications, namely the nRF24 module and OLED display libraries, and follows the same file structure; the \textit{'Inc'} folder contains header files and the \textit{'Src'} folder source files. Icons used on the OLED display are in the dedicated \textit{'logos'} folder inside the \textit{'Inc'} folder.
\newpage
In addition, there are three important files:
\begin{itemize}
	\item \begin{description}
\item[\textit{'project\_tamiya.h'}:]
Shared header located in the \textit{'shared\_libs/Inc'} folder. It contains common libraries and \textit{'platform.h'} file. More importantly, it contains nRF24 communication settings, various macros, and shared function declarations, namely nRF24 and OLED wrapper functions and functions used for UART debug prints.
\end{description}

	\item \begin{description}
\item[\textit{'project\_tamiya.c'}:]
Source file located in the \textit{'shared\_libs/Src'} folder. It consists of function definitions from the appropriate header file.
\end{description}

	\item \begin{description}
\item[\textit{'platform.h'}:]
This header file is in both applications' \textit{'Inc'} folder, contains platform-specific macros and settings, and includes platform-specific headers.
\end{description}
\end{itemize}
The visualization of the file structure with highlighted important files is below.

\begin{forest}
  pic dir tree,
  pic root,
  for tree={% folder icons by default; override using file for file icons
    directory,
  },
  [Software
    [Car, label=right:Main folder of the car control application
    		[Inc
    			[platform.h, file
    			]
    		]
    ]
    [shared\_libs, label=right:Shared libraries for both applications
    		[Inc
    			[project\_tamiya.h, file
    			]
    		]
    		[Src
    			[project\_tamiya.c, file
    			]
    		]
    ]
    [Transmitter, label=right:Main folder of the transmitter control application
    		[Inc
    			[platform.h, file
    			]
    		]
    ]
  ]
\end{forest}

\subsection{Communication parameters}
Since the communication parameters must be equal in both the car and transmitter to establish the connection, they are placed in the shared \textit{'project\_tamiya.h'} header file.

The control packet payload size is only 4 bytes, and the ACK packet payload is only 3 bytes. In addition, 1 byte CRC is used. Payloads are described in figures \ref{tab:ctrl_payload} and \ref{tab:ack_payload}. CRC and other fields of the \textit{Enhanced ShockBurst} packet are not displayed.

\begin{figure}[ht]
\centering
	\begin{bytefield}[bitwidth=1.2em, bitheight=2em]{32}
        \bitheader{0, 8, 16, 24, 32} \\
        \bitbox{16}{Throttle} & \bitbox{16}{Steering}
    \end{bytefield}
    \caption{Control payload format}
    \label{tab:ctrl_payload}
\end{figure}
	
\begin{figure}[ht]
\centering
	\begin{bytefield}[bitwidth=1.5em, bitheight=\widthof{~\small$\frac{1}{2}$\unit{\celsius}~}]{24}
        \bitheader{0, 8, 16, 17, 24} \\
        \begin{rightwordgroup}{RTP \\  Header}
        \bitbox{16}{Battery voltage} & \bitbox{1}{\rotatebox{90}{\small$\frac{1}{2}$\unit{\celsius}}} & \bitbox{7}{Integer temperature}
    \end{bytefield}
    \caption{ACK payload format}
    \label{tab:ack_payload}
\end{figure}
\noindent
Bit 16 of the ACK payload is related to the trick described in \ref{sub:integers}.

The channel frequency is set to \SI{2515}{\MHz} to reduce interferences with the wi-fi signal, and the data rate is the lowest possible \SI{250}{\kilo\bit\per\second}. According to \cite{nrf_datasheet}, a lower air data rate gives better receiver sensitivity than a higher air data rate. Transmitting power is, on the other hand, the highest possible. This setup ensures the most extended potential range.

\section{Transmitter}
\subsection{Peripherals and pin configuration}
\label{sub:tx_conf}
\begin{figure}[h]
\centering
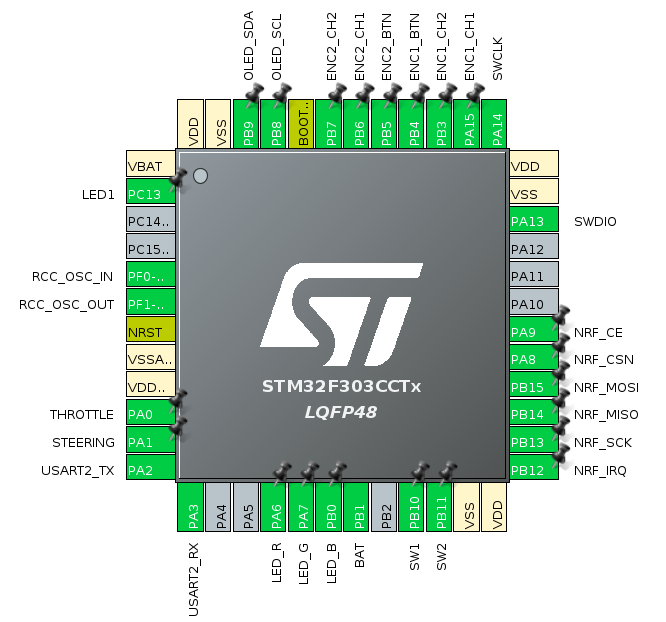
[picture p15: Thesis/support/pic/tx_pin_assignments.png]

\caption{Transmitter pin assignments}
\label{fig:tx_conf}
\end{figure}
\noindent
The microcontroller runs at \SI{72}{\MHz} with a clock source set to a \SI{12}{\MHz} external crystal oscillator.

ADC1 channels 1 and 2 are used to measure the output voltage from control potentiometers. ADC operates with 12-bit resolution in continuous conversion mode with DMA enabled in circular mode with continuous requests to manipulate the data. Once the ADC conversion is started, it remains active, and DMA repeatedly fills the buffer with measured data. Sampling time is the highest possible $601.5$ cycles, and software averaging is used to acquire stable measurements.

ADC3 uses channel 1 to measure the LiPo battery voltage and channel Vrefint to measure the internal reference voltage. Again, the resolution is 12-bit, continuous conversion mode is enabled, and DMA is utilized to transfer data from peripheral to memory. In this mode, the ADC remains active until DMA fills the whole data buffer. The sampling time for channel 1 is $601.5$ cycles, and for channel Vrefint $181.5$ cycles.

The communication module is connected to the SPI2 bus operating in full-duplex master mode. Baud rate is set to \SI{9}{\mega\bit\per\second}, and the data size is standard 8 bits. 'NRF\_IRQ' pin is configured in external interrupt mode with rising edge detection. The rest of the 'NRF' pins are simple outputs.

Quadrature rotary encoders utilize timers TIM2 and TIM4, which are in Encoder mode. This mode is designed specially to interface quadrature encoders with out-of-phase output signals. Encoder push-button pins are configured in external interrupt mode with rising edge detection.

SW1 and SW2 pins belong to the DIP switch and are configured in external interrupt mode with both rising and falling edge detection.

USART2 peripheral is configured as debug serial port. Baud rate is set to \SI{921600}{\bit\per\second} with 8~bits word length and one stop bit.

I2C1 in Fast Mode Plus with a frequency of \SI{1}{\MHz} connects the OLED display. LED pins are simple outputs. Furthermore, TIM6 at \SI{1}{\Hz} and TIM16 at \SI{4}{\Hz}, both timers with interrupts enabled, are used for basic timing purposes.

Figure \ref{fig:tx_conf} shows the complete pinout in STM32CubeMX.

\subsection{Application start}
The program starts with auto-generated initialization of all necessary peripherals. Debug UART is enabled after start by default. Afterward, an orange LED visible from the backside of the transmitter is turned on to indicate application initialization.

First, the OLED display is initialized, and the project logo is displayed. At the same time, a greeting is sent via UART, and the RGB LED flashes through each channel. Automatic self-calibration of both ADCs follows, and the Vrefint calibration value is obtained from the appropriate register. This value is later used to calculate VDDA. Then the communication module is initialized in transmitter mode with parameters defined in \textit{'project\_tamiya.h'}.

After that, the ADC responsible for reading values of control potentiometers is started in circular DMA mode, as described in section \ref{sub:tx_conf}. Processing of the data is explained in section \ref{sub:adc}.

In the final part of initialization, all the timers, including the timers used for quadrature encoders, are started in interrupt mode. Then the UART is deinitialized depending on the Switch1 state, the orange LED is turned off to indicate that initialization is done, and the program enters the main control loop.

\subsection{Main control loop}
The control loop is designed to be as non-blocking and interrupt-driven as possible. Therefore, it consists of a set of 'if' blocks. However, some parts remained blocking. The reason is some of the drivers are blocking and do not allow the use of DMA. Rewriting them was hardly possible or too time-consuming. This is especially true for OLED refreshing, which takes the longest time. Execution of given 'if' block is controlled by flags, internally boolean values, set by appropriate interrupt routines.
\newpage
\begin{itemize}
	\item \begin{description}
\item[\textit{'trigger\_data\_rdy'}:]
The flag is set by ADC interrupt routines and indicates available control values. This block processes and averages measured values from control potentiometers and recalculates them using hardware limits for direct usage in the car. The flag is reset at the end of the block.
\end{description}

	\item \begin{description}
\item[\textit{'adc\_data\_bat\_rdy'}:]
This block is similar to the previous block and indicates available voltage measurements.  First, it averages the measured $Vrefint_{meas}$ and battery voltage data. The next step is VDDA calculation:
\begin{equation}
	V_{DDA} = \frac{\SI{3.3}{\V} \cdot Vrefint_{cal}}{Vrefint_{meas}}\ ,
\end{equation}
where $Vrefint_{cal}$ is a value acquired during the manufacturing process at $V_{DDA} = \SI{3.3}{\V}$ and obtained from the register, and $Vrefint_{meas}$ is measured internal reference voltage. The formula was taken from Section 15.3.32 in \cite{f303_ref}. This computed value is used to convert the ADC battery measurement to the actual voltage.

The corresponding ADC sets the flag, and the program resets it at the end of the block. A~\SI{4}{\Hz} timer triggers the ADC measurement itself.
\end{description}

	\item \begin{description}
\item[\textit{'sending'}:]
This is the first phase of the non-blocking packet transmission routine. It is executed only if the flag is false, indicating that the previous transmission is completed. First, the flag is set, trimming values are added to the control values from potentiometers, and a 4-byte data packet is formed. After that, packet transmission is started. The flag remains set.
\end{description}

	\item \begin{description}
\item[\textit{'NRF\_IRQ'}:]
This is the second, final phase of the packet transmission routine. The communication module's interrupt pin sets the flag once it finishes the transmission. The routine starts with checking the transmission status and reading the received payload. If the payload has the expected size, it is parsed into related variables. Then actions depending on the transmission status follow.

The corresponding counter variable is incremented if the module has reached the maximum retransmit count. This variable is used to detect signal loss as described in section \ref{sub:tx_sig_loss}. If the transmission was successful, the previously mentioned variable is reset, the command frequency counter is incremented, and the status LED is toggled.

The last step is resetting both the \textit{'NRF\_IRQ'} and \textit{'sending'} flags.
\end{description}

	\item \begin{description}
\item[\textit{'display\_refresh'}:]
This section is responsible for refreshing the information on the OLED display. An interrupt routine of a \SI{4}{\Hz} timer sets the flag, and the program resets it at the end of the block. Therefore, the display runs with a framerate of about \SI{4}{FPS}.
\end{description}

	\item \begin{description}
\item[\textit{'ENCx\_IRQ'}:]
This section is executed when the rotary encoder's control timer triggers the interrupt routine upon detecting rotation. Depending on the direction of rotation, the trimming value is increased or decreased. The flag is reset at the end of the block.

Each encoder has its own control block modifying the appropriate trimming value.
\end{description}

	\item \begin{description}
\item[\textit{'ENCx\_reset'}:]
This flag is set by the encoder's push-button. The purpose is to reset the appropriate trimming value to zero. At the end of the block, the flag is reset.
\end{description}

\end{itemize}

\subsection{ADC data processing}
\label{sub:adc}
A feature similar to 'double buffering' is implemented to process data from ADC in circular mode. It is not implemented as two separate buffers but as a single 1024 bytes long buffer. It utilizes the ADC's ability to send notifications when the buffer is half-full and when it is full.

ADC is enabled and DMA starts filling the buffer with data. Once the buffer is half-full, the appropriate interrupt is triggered, and MCU is signaled to start processing the first half of the buffer. The DMA still fills the buffer with new data.

When the DMA fills the buffer completely, the appropriate interrupt is triggered, and the DMA starts filling the buffer from the beginning with new measurements. This state is again signaled to the MCU, which starts processing the second half of the buffer while the DMA fills the first half.

Whether the first or the second half is to be processed is controlled by an integer offset that is set in the interrupt routine. Hence, this method is fast as the DMA still fills the same buffer and does not need to be reconfigured, which would add additional overhead.

This approach is repeated, ensuring that the new measurements do not overwrite the values already in the buffer and, therefore, do not affect the value obtained.

\subsection{Signal quality and loss detection}
\label{sub:tx_sig_loss}
The nRF24 communication module does not support any detailed form of RSSI (Received Signal Strength Indicator). The only information obtainable from the module is whether the signal during the last transmission was below or under a certain threshold. Therefore, a simple signal quality indicator is implemented in the software.

After every successful packet transmission, the counter variable \textit{'tx\_freq\_cnt'} is incremented. During the callback routine of a \SI{1}{\Hz} timer, this value is copied into \textit{'tx\_freq'} variable and displayed. This value, expressing the number of packets per second, is used to measure the signal quality. Thresholds were determined experimentally based on the maximum observed number of packets per second.

Since the detection of signal loss by the transmitter is not as important as in the case of a car and serves mainly for information purposes, the implementation is quite simple.

It depends on the counter variable \textit{'retransmits\_in\_row'}, which is incremented whenever the communication module reaches the maximum number of packet retransmits and reset if the transmission was successful. When this variable is greater than 15, it is evaluated as a signal loss in the \SI{4}{\Hz} timer interrupt routine, and the corresponding flag is set.

This status is visualized on the OLED screen and by changing the color of the status LED to blue.

\subsection{Status visualization}
Both the RGB LED and OLED display are used to visualize the current status. The reasons for the choice are discussed in section \ref{sec:hw_status}.

The RGB LED is clearly visible and serves as a quick notification of the communication and the transmitter's battery status. Color options and their meaning are described in table \ref{tab:led_status}.
\begin{table}[h]
   \renewcommand{\arraystretch}{1.1}
   \centering
    \caption{Explanation of LED status}\label{tab:led_status}   
    \begin{tabular}{c c c}
       \noalign{\hrule height 1.1pt}\noalign{\smallskip}
	   \bfseries RGB LED & \bfseries Communication status & \bfseries Battery status\\[0.2em]
	\noalign{\hrule height 1.1pt}\noalign{\smallskip}     
flashing green	& OK				& $>\,$\SI{6.8}{\V} \\
flashing red		& OK				& $<\,$\SI{6.8}{\V} \\
blue				& signal lost	& --	\\
       \noalign{\smallskip}\noalign{\hrule height 1.1pt}
    \end{tabular}
\end{table} 

The small OLED display is more demanding for quick orientation in the displayed data. On the other hand, it provides more information about the transmitter and even the car. The display interface is divided into two main parts.

The first in the upper part of the display resembles a status bar and provides information about the car, as indicated by the icons: the BLDC temperature and battery state. In case of signal loss, this information is displayed here.

The rest of the screen is separated by a line and belongs to the transmitter status. Information about the current position of control potentiometers is displayed in the middle, along with the trim values. The position of potentiometers is not expressed relatively in percentage. Instead, the actual value sent to the car is displayed. The bottom part offers information about packets per second and the transmitter's battery status.

Both battery indicators are interactive and, depending on the voltage, up to 4 bars are displayed. If the battery voltage drops below the threshold of \SI{6.8}{\V}, a flashing exclamation mark is displayed in the battery logo instead. The signal quality indicator is also interactive.

All logos were created in GIMP and exported as XBM files. These were later 'converted' to header files by changing the file extension. Examples of the display interface are in figure \ref{fig:tx_oled}.
\begin{figure}[h]
    \centering
    \begin{subfigure}{0.35\textwidth}
    \centering
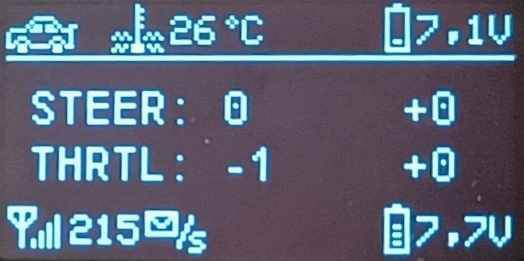
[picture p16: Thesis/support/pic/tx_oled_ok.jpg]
        
%		\caption{front side}
    \end{subfigure}%
    \hspace{1cm}
    \begin{subfigure}{0.35\textwidth}
    \centering
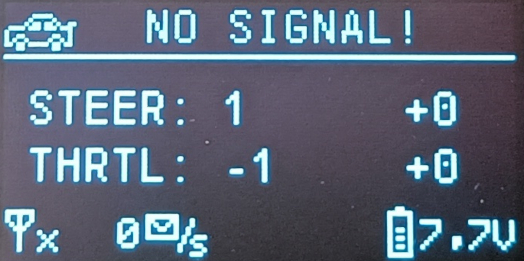
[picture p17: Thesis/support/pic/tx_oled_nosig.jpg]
		
%		\caption{back side}
    \end{subfigure}
	\caption{OLED display interface in transmitter}
    \label{fig:tx_oled}
\end{figure}

\subsection{UART debug prints}
One of the UARTs is utilized for printing debug information. Corresponding pins are available on the connector J3; configuration is in section \ref{sub:tx_conf}.

The printing is enabled by default after the application start and prints the initialization progress. Afterward, the printing is dependent on the state of the Switch1 (the first lever on the DIP switch SW2).

The UART is deinitialized before entering the main control loop if the switch is in the off position or stays initialized otherwise. If debug prints are enabled, the transmitter informs about:
\newpage
\begin{itemize}
\item LiPo battery voltage and VDDA voltage whenever new data is available,
\item encoder rotation,
\item switch position change,
\item no signal state.
\end{itemize}
Debug printing can be enabled or disabled anytime during the application execution.

\section{Car}
\subsection{Peripherals and pin configuration}
\label{sub:car_conf}
\begin{figure}[h]
\centering
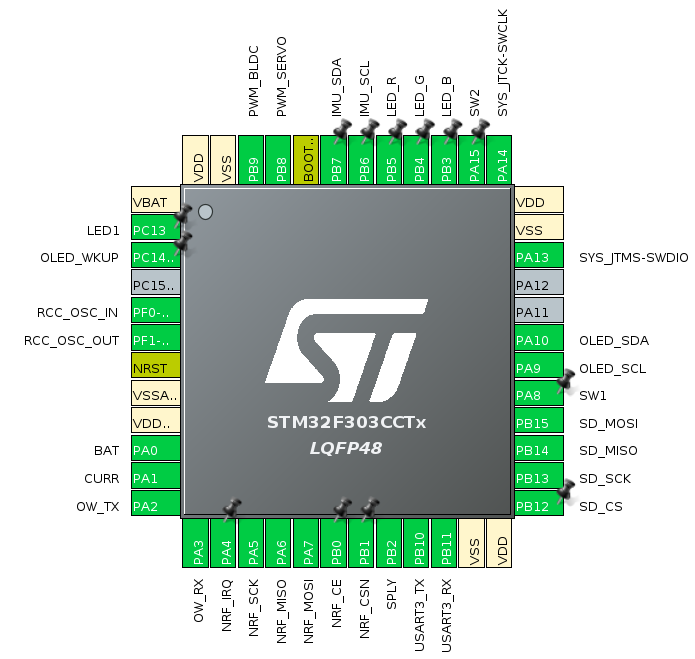
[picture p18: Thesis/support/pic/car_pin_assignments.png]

\caption{Car pin assignments}
\label{fig:car_conf}
\end{figure}
Some of the settings are similar to transmitter settings since both microcontrollers are the same STM32F303CCT6. The microcontroller runs at \SI{72}{\MHz} with a clock source set to an \SI{8}{\MHz} external crystal oscillator.

Channels 2 and 3 of timer TIM8 are used to generate PWM and therefore control the car. Prescaler and counter period values are calculated to represent the pulse width in microseconds. That means the counter value of e.g. $1500$ equals \SI{1500}{\micro\second} pulse width, which is convenient for control application implementation.

ADC1 channels 1 and 2 are used to measure the LiPo battery voltage and output voltage from the current sensor. ADC operates with 12-bit resolution in continuous conversion mode with DMA enabled. Sampling time is again the highest possible $601.5$ cycles to acquire stable measurements.

ADC2 measures the Vrefint channel to obtain the internal reference voltage and channel 12 to obtain the BEC output voltage. The resolution is also 12-bit, and continuous conversion mode with DMA is enabled. The sampling time for channel Vrefint is $181.5$ cycles and $601.5$ cycles for channel~12.

The communication module is connected to the SPI1 bus operating in full-duplex master mode. Baud rate is set to \SI{9}{\mega\bit\per\second}, and the data size is standard 8 bits. 'NRF\_IRQ' pin is configured in external interrupt mode with rising edge detection. The rest of the 'NRF' pins are simple outputs.

As STM32F303 does not support the SDIO interface, the SD card is connected via the SPI2 peripheral. The baud rate is only \SI{281.25}{\kilo\bit\per\second} after reset, but once the SD card is initialized, it is increased to \SI{9}{\mega\bit\per\second}.

I2C2 in Fast Mode Plus with a frequency of \SI{1}{\MHz} connects the OLED display. IMU unit is served by I2C1 in Fast Mode with a frequency of \SI{400}{\kHz}.

1-Wire bus necessary to communicate with the DS18B20 temperature sensor is implemented using USART2 peripheral and DMA. This method is described in \cite{1wire_uart}, and the DMA version was implemented with the help of \cite{1wire_uart_imp}. Since RX and TX pins are tied together, and TX pin is configured as push-pull, it is protected with a diode. This method is much simpler and requires fewer external components than the approach in \cite{1wire_uart} with a discrete open-drain buffer.

SW1 and SW2 pins belong to the DIP switch and are configured in external interrupt mode with both rising and falling edge detection.

USART3 peripheral is configured as debug serial port. Baud rate is set to \SI{921600}{\bit\per\second} with 8~bits word length and one stop bit.

LED pins are simple outputs. Pins PA11 and PA12 are not used in the project's current state but are reserved for a USB peripheral for possible future expansion with a control computer.

Figure \ref{fig:car_conf} shows the complete pinout in STM32CubeMX.

\subsection{Application start}
The application for controlling the car is written similarly to the transmitter. The program starts with the initialization of all peripherals. Debug UART is enabled after start by default, too, and a blue LED on the BlackPill board indicates application initialization.

First, the OLED display is initialized, and the project logo is displayed. At the same time and a greeting is sent via UART. If the Switch2 is turned on, IMU is initialized, and the flag controlling SD card logging is set. The next step is enabling servo and motor PWMs, initializing 1-Wire, and flashing individual channels of RGB LED.

Automatic self-calibration of both ADCs follows, and the Vrefint calibration value is obtained from the appropriate register. This value is later used to calculate VDDA. Then the communication module is initialized in receiver mode with parameters defined in \textit{'project\_tamiya.h'}.

After that, depending on the Switch2 position, the SD card is initialized and mounted. This process is explained in more detail in section \ref{sub:sd_log}.

Lastly, all the timers are started in interrupt mode. Timer TIM15 controlling the display timeout is immediately stopped afterward. This is because the timer triggers an interrupt when started for the first time even though it is not supposed to, which interferes with the display timeout feature.

Then the OLED display is turned off, UART is deinitialized depending on the Switch1 state, and the blue LED is turned off to indicate that initialization is done. The run time in milliseconds is stored just before entering the main control loop for possible later calculation of the data timestamp.

\subsection{Main control loop}
The following section describes the control loop. Similar to the transmitter control loop, it is designed to be as non-blocking and interrupt-driven as possible and consists of a set of 'if' blocks accordingly. The biggest bottleneck is the FatFs driver used for SD card logging, which is too complex to rewrite in DMA mode and takes the longest execution time. Individual 'if' blocks are controlled by their appropriate flag.

\begin{itemize}
	\item \begin{description}
\item[\textit{'NRF\_IRQ'}:]
The flag is set by the communication module and indicates the module's status change. If the status represents newly received data, an ACK packet is first prepared and sent back to the transmitter to confirm successful reception. If the received data has the expected size, processing follows.

Received values are checked against the defined chassis mechanical limits and clipped if they exceed the allowed range. After that, values are recalculated to pulse widths and set into PWM generating timers. Lastly, the safety timer is reset, and the command frequency counter is incremented. The flag is reset by the program at the end of the block.
\end{description}

	\item \begin{description}
\item[\textit{'temp\_conv\_ready'}:]
Although it may seem like the temperature sensor controls this flag, it is actually controlled by a \SI{1}{\Hz} timer. The temperature sensor datasheet states that temperature conversion with 12-bit resolution takes \SI{750}{\ms} and, therefore, one-second intervals are sufficient.

Nevertheless, this section indicates that the temperature conversion is done, and the reading process can be started. If SD logging is enabled, it also flushes cached data to the SD card with the \textit{'f\_sync'} function.
\end{description}

	\item \begin{description}
\item[\textit{'temp\_received'}:]
This is the section controlled by the temperature sensor. The flag is set by a~\mbox{1-Wire} interrupt and indicates that the measured data transfer from the sensor has finished. Thus the raw register data is converted to the actual temperature. The process is mentioned in section \ref{sub:integers}.

Lastly, the flag is reset, and the following temperature conversion is initialized.
\end{description}

	\item \begin{description}
\item[\textit{'adc\_data\_bat\_rdy'} and \textit{'adc\_data\_sply\_rdy'}:]
Appropriate ADC callback routines set flags. Both of them must be set to execute this block, which is responsible for processing data. First, measurements from both ADCs are averaged to obtain stable values. The VDDA calculation and conversion of values to the relevant physical quantities follows. Then if SD logging is enabled, data from IMU is read, and all the values are formatted and written to the SD card.

At the end of the block, both flags are reset. A \SI{50}{\Hz} timer triggers ADCs themselves.
\end{description}

	\item \begin{description}
\item[\textit{'log\_data'} and \textit{'unmount\_sd'}:]
This block ensures safe unmount and disconnection of the SD card. The file is truncated, closed, and the SD card is unmounted. If Switch2 is turned on after the start of the application, the \textit{'log\_data'} flag is set. The \textit{'unmount\_sd'} flag is set if it is turned off during execution. Both flags are reset at the end of the block.
\end{description}

	\item \begin{description}
\item[\textit{'display\_refresh'} and \textit{'display\_wakeup'}:]
This section is responsible for refreshing the information on the OLED display if it is turned on. An interrupt routine of a \SI{4}{\Hz} timer sets the \textit{'display\_refresh'} flag, and the program resets it at the end of the block. The \textit{'display\_wakeup'} flag is set for 5 seconds by pressing the push-button under the display, which also activates it.
\end{description}

\end{itemize}

\subsection{Integer arithmetics}
\label{sub:integers}
Although the selected MCU contains the FPU, all program variables are integers. The problem is not the speed of floating-point operations. Floating-point operations are fast thanks to the FPU and are used in some parts of the program, mainly during converting ADC value to actual voltage.

The problem is that formatting floats for output is slow and, in addition, requires a special flag for the linker and increases the final file size considerably. Hence, float variables are multiplied by~1000 to maintain at least some accuracy and saved as an integer. This approach applies mainly to the accelerometer data. The battery voltage value is already calculated in millivolts to avoid float variables altogether.

An easy 'trick' is utilized to display the BLDC temperature as a decimal number without float variables. The raw register data is converted to the integer part of the temperature using bits 11 to 4, according to Figure 4 in \cite{ds_datasheet}. Then the program checks the value of bit 3 associated with $2^{-1} = \frac{1}{2}$\unit{\celsius} and sets another integer variable to 5 or 0 accordingly. Afterward, the temperature is displayed as two integers with a point between them.

\subsection{Signal quality and loss detection}
\label{sub:safety}
It is expected from an RC vehicle that it safely stops or at least stops the motor in case of signal loss to prevent damage or injury. Since pulse width values controlling the servo and motor are only updated when a new control packet is received, loss of the signal would mean that the last command remains set in PWM generating timer and the car uncontrollably drives away.

One of the timers is used as a 'safety timer' to solve this behavior. The timer is set to \SI{4}{\Hz} with interrupts enabled, and its counter is reset whenever a command packet is successfully received. If no new command is received within \SI{250}{\ms}, the timer triggers an interrupt, resetting the motor and servo to their 'neutral' position and setting the \textit{'no\_signal'} flag. 

Moreover, the associated interrupt callback routine is the only one that directly interferes with car control, which ensures the motor is always reset after exactly \SI{250}{\ms} independently of the current program state if no new command is received.

Theoretically, one of the watchdogs could have been used instead of the timer as a more robust safety measure. However, not reloading it in time would mean restarting the MCU and interfering with SD card data logging.

The signal quality indicator is implemented identically to the transmitter. Each time the packet is successfully received, a counter variable is incremented. The value of the counter variable is copied to another variable and reset every second by a \SI{1}{\Hz} timer. This value is used to estimate signal quality, which is then visualized on the OLED display.

\subsection{SD logging}
\label{sub:sd_log}
A micro SD card slot is ready to use to record driving data. The application implements \textit{ChaN's} FatFs driver to interface the SD card, and therefore, any FAT-formatted micro SD card can be used. Driving data are saved with a frequency of \SI{50}{\Hz} in CSV file format.

The logged data includes a timestamp, voltage and current measurements, BLDC temperature, actuator control values, and IMU data. The exact format and corresponding units of quantities are always specified in the first two lines of the CSV file. An example of the data output is shown in figure \ref{fig:data_raw}.

Data logging is enabled if Switch2 is turned on during the application start. Unlike UART prints, it cannot be enabled anytime. Depending on the Switch2 position, the SD card mounting and preparation procedure is performed right after communication module initialization.
\begin{figure}[h]
\centering
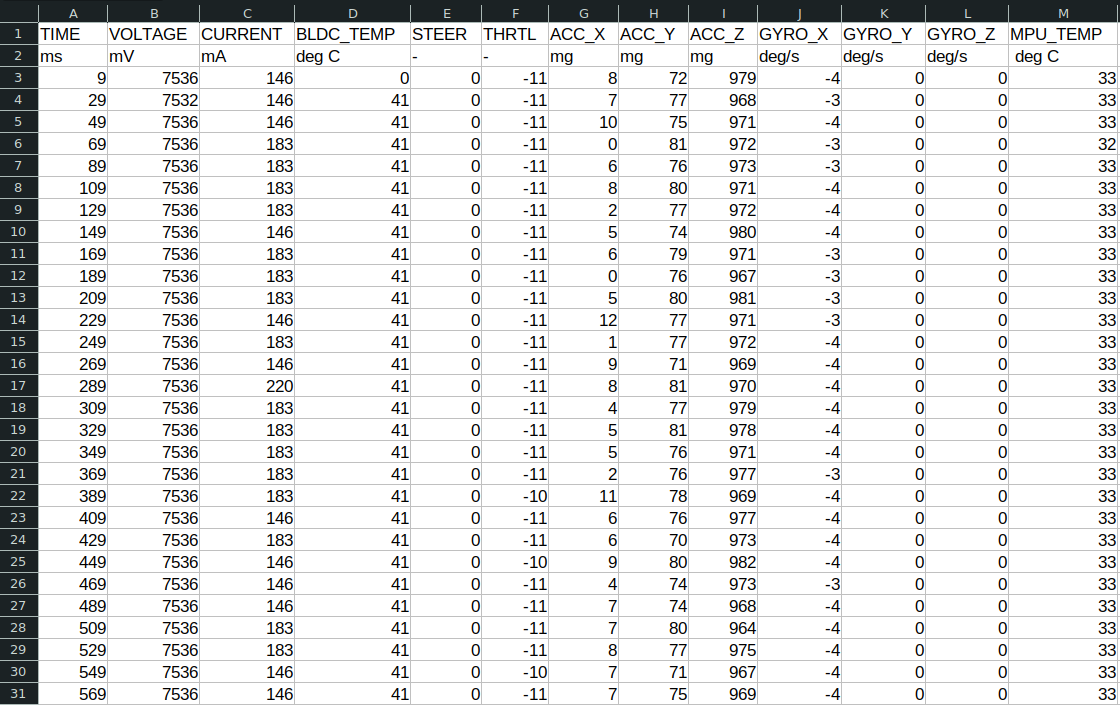
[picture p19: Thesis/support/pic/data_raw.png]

\caption{Example of raw data}
\label{fig:data_raw}
\end{figure}

It starts with mounting the disk and printing SD card statistics. Then the application search for the \textit{'logs'} folder, and if it is not found, it creates one. Afterward, the files in the folder are counted to determine the log number, and a new file is created.

Then pre-allocation of \SI{10}{\mebi\byte} of memory follows, which should suffice for approximately an \mbox{hour-long} log file. This step is critical as it dramatically decreases filesystem overhead when writing to the file. Without the pre-allocation, the \textit{'f\_sync'} function sometime took so long that the safety timer triggered and reset the motor.

Every second, the log file is \textit{'f\_synced'} to lower its execution time and prevent data loss if an unexpected event happens, such as a shutdown. With this approach, the user should not lose more than the last second of data.

Even though the pre-allocation reduced \textit{'f\_sync'} execution time significantly, it still sometimes takes more than \SI{100}{\ms}, meaning that some data are missing from the log.

Switch2 must be turned off to finish data logging properly. After that, the file is truncated and closed, and the whole SD card is safely unmounted.

\subsection{Status visualization}
Visualization of the status is consistent with the transmitter and utilizes the RGB LED and a bit smaller OLED display. Again, the RGB LED serves as a quick notification of the communication and the car's battery status. In the case of body shell mounting, it is also visible through it and is the only status indicator. The color scheme is the same as in the transmitter, and thus, the same table \ref{tab:led_status} applies.

Since the car is usually driven with a body shell mounted, the display is not visible to the user as it is under the body on the control board. For this reason, the display is turned off the majority of the time. It is activated only during the start of the application to display the project logo. The display can be turned on anytime by pressing the push-button under the display, waking it up for 5 seconds.

The display interface is much more plain than the one in the transmitter. 
Due to the size of the display, the only information presented is the battery voltage, motor temperature, and signal quality indicator with packets per second. Both battery and signal indicators are interactive again.

The signal loss is visualized only by the RGB LED and the zero frequency of the commands on the OLED display; no dedicated error message is shown. Examples of the display interface are in figure \ref{fig:car_oled}.
\begin{figure}[h]
    \centering
    \begin{subfigure}{0.4\textwidth}
    \centering
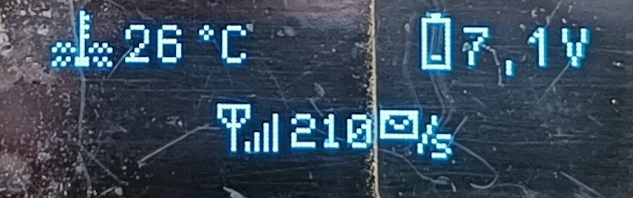
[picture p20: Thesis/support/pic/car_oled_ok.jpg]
        
%		\caption{front side}
    \end{subfigure}%
    \hspace{1cm}
    \begin{subfigure}{0.4\textwidth}
    \centering
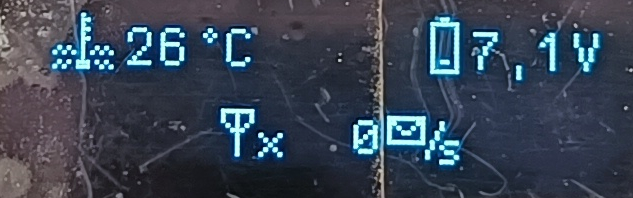
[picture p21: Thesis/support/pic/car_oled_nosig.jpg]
		
%		\caption{back side}
    \end{subfigure}
	\caption{OLED display interface in car}
    \label{fig:car_oled}
\end{figure}

\subsection{UART debug prints}
One of the UARTs is reserved for printing debug information. Corresponding pins are available on the pin header under the display; configuration is in section \ref{sub:car_conf}. The behavior is the same as in the transmitter.

The printing is enabled by default after the application start and prints the initialization progress. Afterward, the printing is dependent on the state of the Switch1.

The UART is deinitialized before entering the main control loop if the switch is in the off position or stays initialized otherwise. If debug prints are enabled, the car informs about:
\begin{itemize}
\item LiPo battery voltage and current, VDDA voltage, \SI{5}{\V} supply voltage, and BLDC temperature whenever new data is available,
\item file sync, save, write error if SD logging is enabled,
\item switch position changes and push-button presses,
\item no signal state.
\end{itemize}
Debug printing can be enabled or disabled anytime during the application execution.

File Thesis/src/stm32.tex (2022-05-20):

%!TEX ROOT=main.tex

\part{STM32 microcontrollers}
\label{chap:STM}
\section{Introduction}
\label{sec:stm_intro}
STM32 is a family of 32-bit microcontrollers by STMicroelectronics based on ARM Cortex-M processor, namely Cortex-M3, Cortex-M4(F), Cortex-M0, Cortex-M0+, Cortex-M7F, and Cortex-M33F. The STM32 family consists of numerous series of microcontrollers designed for various use-cases. These can be divided into four main groups: Mainstream, High Performance, Ultra-low-power, and~Wireless series. As every series has specific features and peripherals, this section will only focus on the~main differences between used ARM Cortex cores. Table \ref{tab:cortex} shows the utilization of ARM cores in the particular STM32 series.
%\begin{table}[ht]
%\begin{ctucolortab}
%\begin{tabular}{cc}
%\bfseries ARM Core & \bfseries STM32 series \\\Midrule
%Cortex-M3 & F1, F2, L1 \\ 
%Cortex-M4F & F3, F4, G4, L4, L4+, WB, WL\tablefootnote{Based only on ARM Cortex-M4 (without FPU).} \\	
%Cortex-M0 & F0 \\ 
%Cortex-M0+ & G0, L0 \\
%Cortex-M7F & F7, H7 \\
%Cortex-M33F & L5, U5
%\end{tabular}
%\end{ctucolortab}
%\caption{ARM Core utilization in STM32 family}
%\label{tab:cortex}
%\end{table}

\begin{table}[ht]
   \renewcommand{\arraystretch}{1.1}
   \centering
    \caption{ARM Core utilization in STM32 family}\label{tab:cortex}   
    \begin{tabular}{c c}
       \noalign{\hrule height 1.1pt}\noalign{\smallskip}
	   \bfseries ARM Core & \bfseries STM32 series\\[0.2em]
	\noalign{\hrule height 1.1pt}\noalign{\smallskip}     
Cortex-M3 & F1, F2, L1 \\ 
Cortex-M4F & F3, F4, G4, L4, L4+, WB, WL\tablefootnote{Based only on ARM Cortex-M4 (without FPU).} \\	
Cortex-M0 & F0 \\ 
Cortex-M0+ & G0, L0 \\
Cortex-M7F & F7, H7 \\
Cortex-M33F & L5, U5 \\
       \noalign{\smallskip}\noalign{\hrule height 1.1pt}
    \end{tabular}
\end{table} 

\section{Division by ARM cores}
\label{sec:stm_arm_division}
	\subsection{Cortex-M3}
	\label{sub:stm_m3}
Cortex-M3 was the first processor in the Cortex-M generation and the first core used in the STM32 family in the STM32F1 series of microcontrollers. ARM first released this high-performance processor based on ARMv7-M architecture in 2005. It features modified Harvard architecture (with unified memory space) and a 3-stage pipeline. Thanks to 32-bit addressing, 4GB of memory space is supported \cite{yu}.
	
	\subsection{Cortex-M4F}
	\label{sub:stm_m4}
The successor to Cortex-M3 was released by ARM in 2010. This new generation called Cortex-M4 is similar to its predecessor in design and features. The instruction set now contains DSP (Digital Signal Processor) instructions for more complex data processing, and there is an optional single-precision FPU (Floating Point Unit). Variant with FPU is known as Cortex-M4F \cite{yu}. 
	
	\subsection{Cortex-M0}
	\label{sub:stm_m0}
Cortex-M0 processor is one of the smallest ARM processors available, optimized for small size and low power consumption. The processor is based on ARMv6-M with a smaller instruction set, uses Von Neumann architecture, and has a 3-stage pipeline. This small core is ideal for general data processing tasks, where low cost and high energy efficiency matter \cite{m0_web}.
	
	\subsection{Cortex-M0+}
	\label{sub:stm_m0_plus}
Cortex-M0+ is based on Cortex-M0, thus adopting small a size and further improving power efficiency and performance. The instruction set and tools are fully backward compatible with Cortex-M0. ARM reduced pipeline to 2 stages to lower power consumption. Furthermore, the processor has more options available, such as vector table relocation and memory protection unit (MPU) \cite{m0+_web}.
	
	\subsection{Cortex-M7F}
	\label{sub:stm_m7}
The most powerful processor in the Cortex-M family is Cortex-M7. The processor uses \mbox{ARMv7-M} architecture and features the longest pipeline with six stages. Given the used architecture, the instruction set contains DSP instructions, and there is also an optional FPU, which can be single-precision or even double-precision. Main buses have been enlarged to 64-bit wide. Variant with FPU is known as~Cortex-M7F \cite{m7_web}. 
	
	\subsection{Cortex-M33F}
	\label{sub:stm_m33}
Cortex-M33 is the newest core used in the STM32 family of microcontrollers. The processor is based on more recent ARMv8-M architecture with Harvard bus architecture. It is conceptually similar to Cortex-M4 with a 3-stage pipeline and optional single-precision FPU. The core is ideal for IoT applications as it has optional TrustZone security instructions for hardware-enforced isolation and memory protection unit (MPU). Variant with FPU is known as Cortex-M33F \cite{m33_web}. 

\section{Architecture}
\label{sec:stm_arch}
ARM as a company does not construct microcontrollers but instead designs the core and other components and licenses them to silicon designers. It is the same concept with the STM32 family of microcontrollers - ST Microelectronics obtains the processor design from ARM as a base for their microcontroller. The company then attaches its own set of memories and peripherals, such as ADC (Analog-to-Digital converter), DAC (Digital-to-Analog converter), clock generation and timers, and various types of connectivity peripherals like UART, SPI, I\textsuperscript{2}C, etc.

This approach is illustrated in figure \ref{fig:f303}, which shows the circuit diagram of the STM32F303CC microcontroller used in this project. It shows the Cortex-M4F processor with all the ST-specific peripherals and memories around.
\begin{figure}
\centering
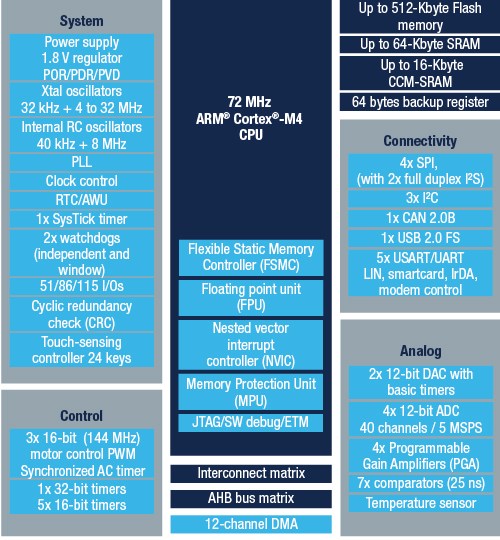
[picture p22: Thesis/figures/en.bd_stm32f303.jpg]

\caption{STM32F303 circuit diagram \cite{f303_diagram}}
\label{fig:f303}
\end{figure}

	\subsection{Clock}
	\label{sub:clock}
The frequency of the processor, buses, and connected peripherals is derived from their clock source, usually an oscillator. STM32 microcontrollers include internal clock sources, or it is possible to connect external clock sources. The frequency from other clock sources can be multiplied by the internal PLL (Phase-Locked Loop) circuit to speed up the microcontroller further and reach higher frequencies. Several prescalers allow finetuning bus and peripherals speed. Internal clock sources have the advantage of providing a clock source at a low cost with no external components. However, being an RC oscillator, the frequency produced is usually not as accurate as an external oscillator.

	\subsection{Interrupts}
	\label{sub:nvic}
The main controller responsible for handling interrupt events is Nested Vectored Interrupt Controller, NVIC for short. It is tightly coupled to the Cortex core allowing for low latency interrupt processing. The NVIC features support for up to 240 interrupt inputs with programmable priorities, which can be individually enabled or disabled, along with Non-Maskable Interrupts (NMI). Furthermore, in the case of Cortex M3 and M4, the interrupt latency is only 12 cycles with zero wait state memory \cite{yu}. All interrupts can be triggered by software by writing to the appropriate register; this also applies to many system exceptions. Microcontroller vendors determine the total number of interrupts supported by the device with Cortex core when designing the chip.

In the  STM32 family of microcontrollers, there is also a hardware device called extended interrupts and events controller (EXTI). This controller is connected to the NVIC and supports up to 36~external/internal interrupt events. Active edge for external interrupts is programmable. This device makes it possible to generate interrupts or wake-up events from external peripherals and GPIO pins.

	\subsection{Buses}
	\label{sub:buses}
The Cortex core has a well-defined on-chip bus structure and protocol that allows the connection of~various memory configurations and peripherals. Since most of the Cortex cores use Harvard architecture, multiple bus interfaces enable simultaneous access to instructions and data. Buses are (most of the time) 32-bit wide.

The primary bus interface protocol utilized is AHB Lite (Advanced High-performance Bus). This~pipelined protocol allows high operation frequency with a small silicon footprint and is used in program memory and system bus interfaces. Usually, the bus can have more devices that act as a master, for example, DMA (Direct Memory Access) or Ethernet controller. Therefore, the processor includes a bus matrix (or AHB interconnect matrix) that manages transfers from multiple bus masters to different slave segments. Particular bus matrix implementation is shown in figure \ref{fig:f303_busmatrix}.
\begin{figure}[h]
\centering
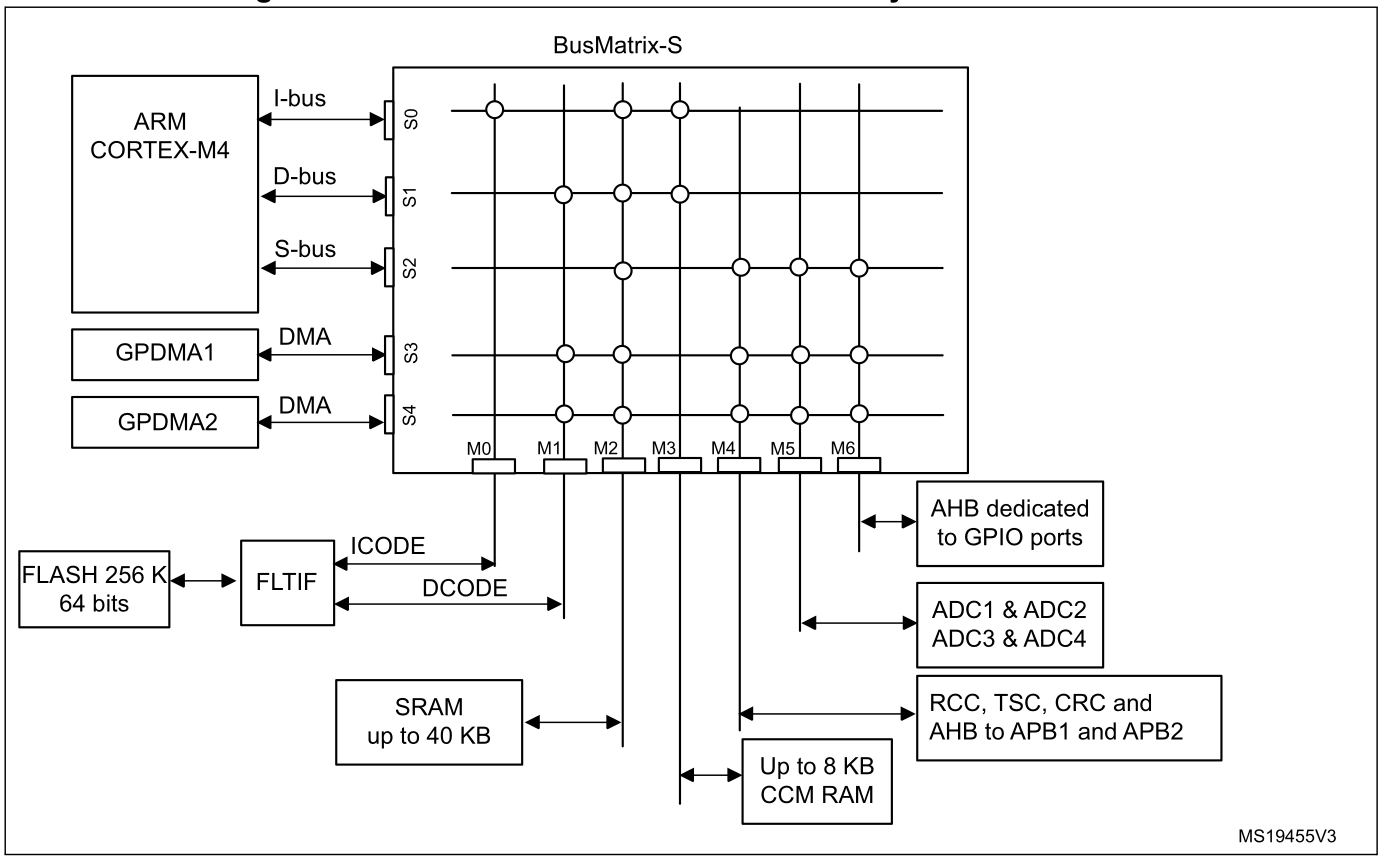
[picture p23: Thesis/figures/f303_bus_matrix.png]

\caption{STM32F303CC bus architecture \cite{f303_ref}}
\label{fig:f303_busmatrix}
\end{figure}

The secondary bus used mainly for connecting peripherals is APB (Advanced Peripheral Bus). Usually, APB buses are connected to the AHB bus matrix using bridge components. If the peripheral needs higher bandwidth and operation speed, for example, the ADC, it is possible to connect it directly to the faster AHB bus.

Some of the more advanced Cortex processors also use other buses. For example, the Cortex-M7 has an additional 64-bit wide AXI bus that can be used for faster FLASH memory access \cite{m7_web}. 

	\subsection{Memories}
	\label{sub:memories}
Thanks to the bus architecture, different memories can easily be attached to the AHB bus with suitable memory interface logic. Even though the bus is 32-bit, there are no width restrictions if appropriate conversion hardware is used.

Usually, types like SRAM and FLASH are often used for data memory and program code memory, respectively. However, there is no real limitation on memory type connected to a processor, and different technologies can be utilized, e.g., SDRAM, EPROM, etc. Also, memory size is not limited. The only requirement is that the memory should be byte-addressable, and the interface has to support byte, half-word, and word transfers \cite{yu}.

	\subsection{Direct Memory Acces (DMA)}
	\label{sub:dma}
A Direct Memory Access is a programmable hardware unit connected to the AHB bus. It reduces processor load by offloading memory transfer operations. Supported transfer directions are peripheral-to-peripheral, memory-to-peripheral, peripheral-to-memory, and also memory-to-memory. There is a small overhead when setting the unit, but afterward, the whole transfer is handled by DMA without processor intervention, thus leaving computing power to other tasks. The unit usually has several independent channels with assignable priorities.

\section{Peripherals}
\label{sec:stm_periph}
Every series of STM32 microcontrollers features different peripherals, from the basic ones with little settings to more advanced and configurable ones. This section is not supposed to be an overly exhausting listing of all the peripherals across all STM32 families, but instead, it focuses mainly on the most used ones and those used in this project.

	\subsection{GPIO}
	\label{sub:gpio}
The abbreviation GPIO stands for General-Purpose Input/Output. It is a designation for microcontroller pins. The pins are arranged in groups of sixteen and are referred to as GPIOx (for example, GPIOA, GPIOC). Not every pin from the group has to be physically present. Especially for microcontrollers with smaller packages, it is usual that some pins from the group are missing. In figure \ref{fig:gpio}, there is a typical internal structure of the GPIO pin with internal protection diodes.

Each pin can be set as either input, output, or alternate function. Internal pull-up and pull-down resistors are available as well. These features are configured and controlled by software. Most GPIO control registers are 32-bit and have to be accessed as 32-bit words, although some STM32 series support half-word and byte access.

If the pin is in alternate function mode, it is controlled by a connected peripheral, for example, ADC, timer, or USART. Thanks to the highly flexible pin multiplexing, many peripheral functions can be remapped to another pin. Debug pins are in alternate function mode by default after microcontroller reset. Other pins are usually in floating input mode.

When the pin is set as output or alternate function, it can be push-pull or open-drain. Most of the pins can provide $\pm20 \text{ mA}$ of current, making it possible to drive, for example, a LED directly. However, the total current that a microcontroller can source or sink is limited. Connecting pins to voltages higher than the supply voltage is not recommended, yet many pins are \SI{5}{\V} tolerant.
\begin{figure}
\centering
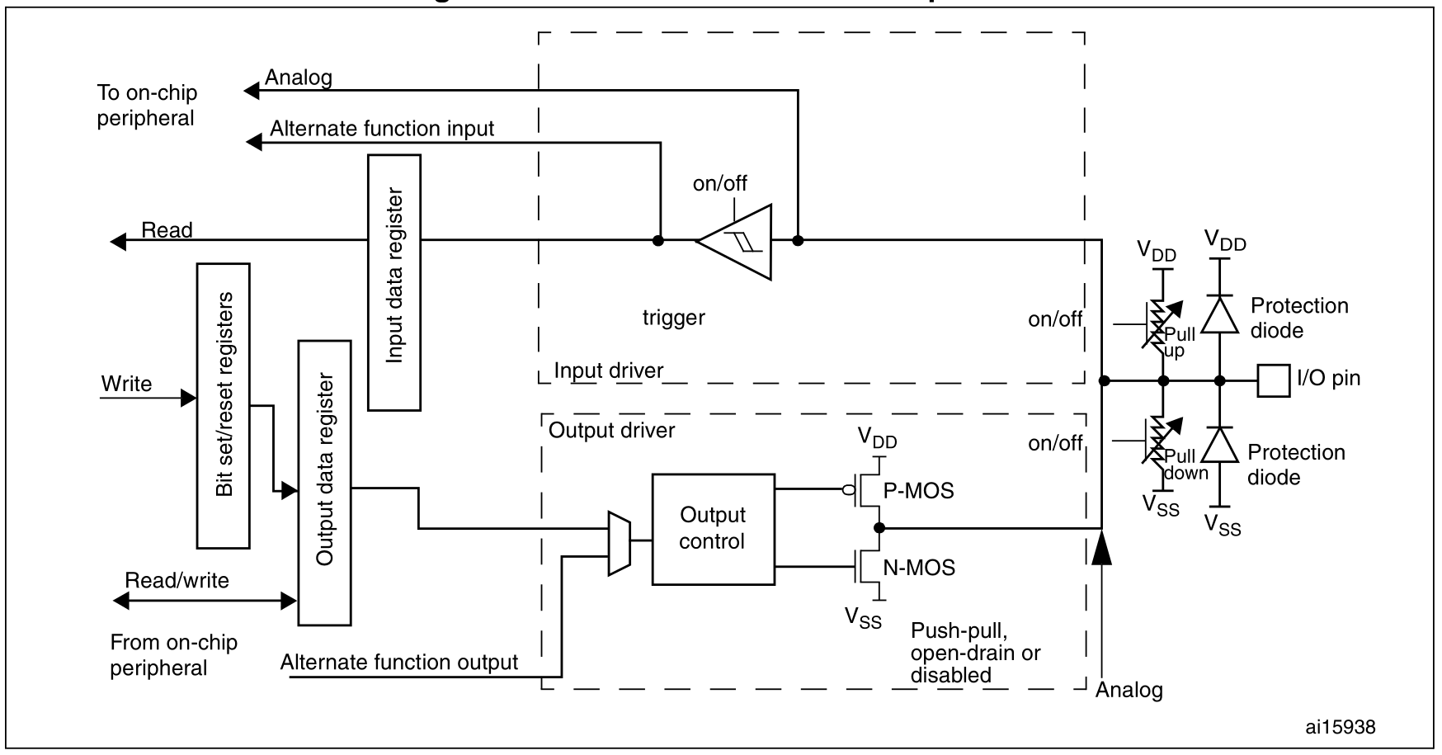
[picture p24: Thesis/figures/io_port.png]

\caption{Basic structure of an I/O port bit \cite{f303_ref}}
\label{fig:gpio}
\end{figure}

	\subsection{Timers}
	\label{sub:timers}
Timers are one of the basic peripherals. The primary function is counting; it can measure time and do a specific action, for example, toggle a pin. The counter clock frequency is adjustable using a programmable prescaler. Usually, there are many timers in the microcontroller with varying features.

The simplest ones are basic timers. These timers are predominantly used for time-base generation as they feature only a simple up counter, usually 16-bit.

The more feature-rich timers are general-purpose timers. With those, besides the basic functionality, it is possible to generate various waveforms or measure the pulse length of the input signal. Furthermore, there can be support for incremental encoders with quadrature output, which can then be connected straight to the MCU. This feature is handy and makes interfacing encoders pretty straightforward.

As the name suggests, the advanced-control timers are the most advanced. Functionality includes all the features of previously mentioned timers with some added or upgraded. Most of the time, advanced-control timers have more channels that can be synchronized together or using an external signal. This ability makes it possible to generate a three-phase PWM output to control a three-phase motor like BLDC.

The Cortex core contains another 24-bit timer called SysTick timer, dedicated to real-time operating systems. It usually provides OS with regular timer interrupts for time-keeping, but it can also be used as a standard down counting timer.

	\subsection{Analog-to-Digital Converter (ADC)}
	\label{sub:st_adc}
Another common peripheral is the Analog-to-Digital converter. This peripheral can convert a given voltage (usually between \SI{0}{\V} and VDDA) to a binary number. One possible utilization can be reading a potentiometer voltage to obtain the trigger position.

The particular implementation can vary between the STM32 series, but most of the time, they use successive-approximation ADC or Sigma-Delta ADC. It can be configured to measure either single-ended input or differential input in continuous or single-shot mode. Also, some internal channels are~available, for example, connected to an internal temperature sensor and voltage reference.

An internal ADC self-calibration is a convenient feature that can compensate for offset and gain error and significantly improve conversion accuracy. The calibration is triggered by software. If the application has to handle a large amount of data, the DMA unit can serve the ADC memory transfers to free the CPU. Moreover, an analog watchdog feature can monitor the converted voltage and generate an interrupt if it exceeds the programmed thresholds. 

	\subsection{Digital-to-Analog Converter (DAC)}
	\label{sub:dac}
The Digital-to-Analog converter does the exact opposite of the Analog-to-Digital converter. It converts the given binary number to a corresponding analog voltage. It is possible to generate complex waveforms or an audio signal with this peripheral. The DAC can therefore be used in many audio applications. If at least two channels are available, the conversion can be independent or simultaneous with external triggers, providing the ability to generate a stereo audio signal. Usually, the DAC also features a noise-wave generation or a triangular-wave generation. Such as with the ADC, the DAC memory transfers can be controlled by DMA, thus freeing up the processor.

	\subsection{Serial Peripheral Interface (SPI)}
	\label{sub:spi}
The serial peripheral interface is a master-slave interface bus used to communicate with smaller devices, such as sensors, memories, displays, or LED drivers. If supported by a particular microcontroller, the peripheral can also be configured as an I\textsuperscript{2}S (Inter-Integrated Sound) interface, allowing the connection of digital audio devices.

Peripheral settings are rich to support a wide range of compatible devices. It can operate either as a master, providing a clock to connected devices, or as a slave; multimaster mode is also possible. Communication mode and speed can be configured as well as frame size and clock polarity. The DMA unit can help handle a lot of data and achieve high data communication rates with hardware control. Moreover, the SPI peripheral includes a hardware CRC unit with automatic CRC error checking. This feature can be helpful when communicating with SD memory cards.

	\subsection{Inter-Integrated Circuit (I\textsuperscript{2}C)}
	\label{sub:i2c}
The Inter-Integrated Circuit is another commonly used short-range communication bus in embedded systems. It is also a synchronous interface that requires fewer communication wires than SPI but~provides lower communication rates. As the SPI interface, the I\textsuperscript{2}C can be used to communicate with small displays, memories, and other rather lower-speed devices.

The peripheral supports both 7-bit and 10-bit addressing modes, programmable analog and digital noise filters, and configurable multiple speed modes depending on the particular microcontroller. Furthermore, the peripheral includes a hardware CRC unit, and it is designed to support SMBus and PMBus protocols used by PCs and servers. DMA channel connecting I\textsuperscript{2}C is also available to provide hardware control of transfers.

	\subsection{USART}
	\label{sub:usart}
USART stands for Universal Synchronous/Asynchronous Receiver/Transmitter. Although computers are rarely equipped with serial ports these days (except for the USB), serial communication is still highly used in the embedded world as it is simple and easy to use. This peripheral is flexible and has a wide range of applications - it can be used for simple UART communication; in the synchronous mode, it can act like SPI master/slave; it also features hardware management of some signals from industry standards like RS-232 and RS-485. Moreover, there is support for Smartcard communication, IrDA serial infrared communication, and multiprocessor communication. It is also possible to use the peripheral to implement other buses with hardware control, for example, Modbus or 1-Wire.  

The peripheral offers many programmable parameters like baud rate, data word length, the number of stop bits, data order, parity control, or oversampling. Furthermore, USART is the source of many interrupts indicating various statuses and flags. The peripheral is connected to the DMA unit like other serial communication peripherals, significantly facilitating the handling of continuous streams or huge amounts of data.

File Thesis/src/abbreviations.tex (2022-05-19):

\section*{List of Abbreviations}
\begin{table}[h]
   \renewcommand{\arraystretch}{1.1}
   \centering
%    \caption{ARM Core utilization in STM32 family}
    \label{tab:abbrev}   
    \begin{tabular}{c c}
       \noalign{\hrule height 1.1pt}\noalign{\smallskip}
	   \bfseries Abbreviation & \bfseries Meaning\\[0.2em]
	\noalign{\hrule height 1.1pt}\noalign{\smallskip}  

API		& Application Programming Interface \\
ACK		& Acknowledgment packet \\ 
ADC		& Analog-to-Digital Converter \\
AHB		& Advanced High-performance Bus \\
APB		& Advanced Peripheral Bus \\
AXI		& Advanced eXtensible Interface \\
BEC		& Battery Eliminator Circuit \\
BLDC		& Brushless DC electric motor \\
CAD		& Computer-Aided Design \\
CRC		& Cyclic Redundancy Check \\
DAC		& Digital-to-Analog Converter \\
DIP		& Dual In-line Package \\
DMA		& Direct Memory Access \\
DSP		& Digital Signal Processor \\
EPROM	& Erasable Programmable Read-Only Memory \\
ESC		& Electronic Speed Controller \\
%EXTI		& External Interrupt/event controller \\		% jednou
FPU		& Floating Point Unit \\
GPIO		& General-Purpose Input/Output \\
I\textsuperscript{2}C	& Inter-Integrated Circuit \\
IMU		& Inertial Measurement Unit \\
LiPo		& Lithium-ion Polymer battery \\
MCU		& Microcontroller Unit \\
%MPU		& Memory Protection Unit \\					% jednou
Ni-Cd	& Nickel-Cadmium battery \\
%NMI		& Non-Maskable Interrupt \\					% jednou
NVIC		& Nested Vectored Interrupt Controller \\	% 3x v jedne sekci
OLED		& Organic Light-Emitting Diode (display type) \\
%OS		& Operating System \\
PCB		& Printed Circuit Board \\
%PLL		& Phase-Locked Loop \\						% jednou
PWM		& Pulse Width Modulation \\
RC		& Radio Control \\ 
SDRAM	& Synchronous Dynamic Random Access Memory \\
SPI		& Serial Peripheral Interface \\
SRAM		& Static Random Access Memory \\
UART		& Universal Asynchronous Receiver and Transmitter \\
%VBAT		& pin for connecting external battery \\
VDDA		& Analog supply voltage pin \\

% ??? AC, DC, USB, TCP/IP, VBAT
       \noalign{\smallskip}\noalign{\hrule height 1.1pt}
    \end{tabular}
\end{table}

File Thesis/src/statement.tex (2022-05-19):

\null \vfill{}
\section*{Prohlášení}
		
%I hereby declare that I have completed this thesis independently and that I have used only
%the sources (literature, software, etc.) listed in the enclosed bibliography.

Prohlašuji, že jsem předloženou práci vypracoval samostatně a že jsem uvedl veškeré použité informační zdroje v souladu s Metodickým pokynem o dodržování etických principů při přípravě vysokoškolských závěrečných prací.\\[0.5cm]

V Praze dne 11. 5. 2015
\begin{figure}[!h]
	\begin{flushright}
		%\includegraphics[width=7cm]{fig/podpis.jpg}
	\end{flushright}
\end{figure}
\\

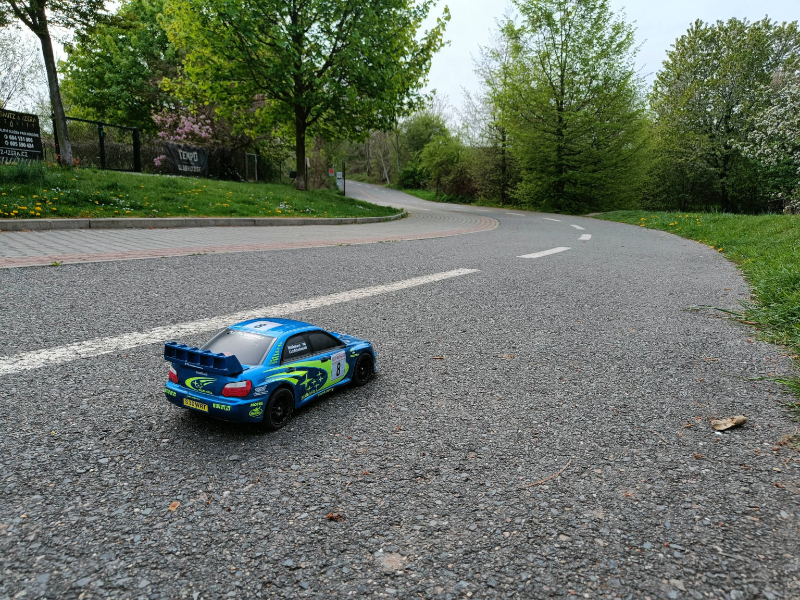
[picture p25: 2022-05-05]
Thesis/support/pic/placeholder.jpg

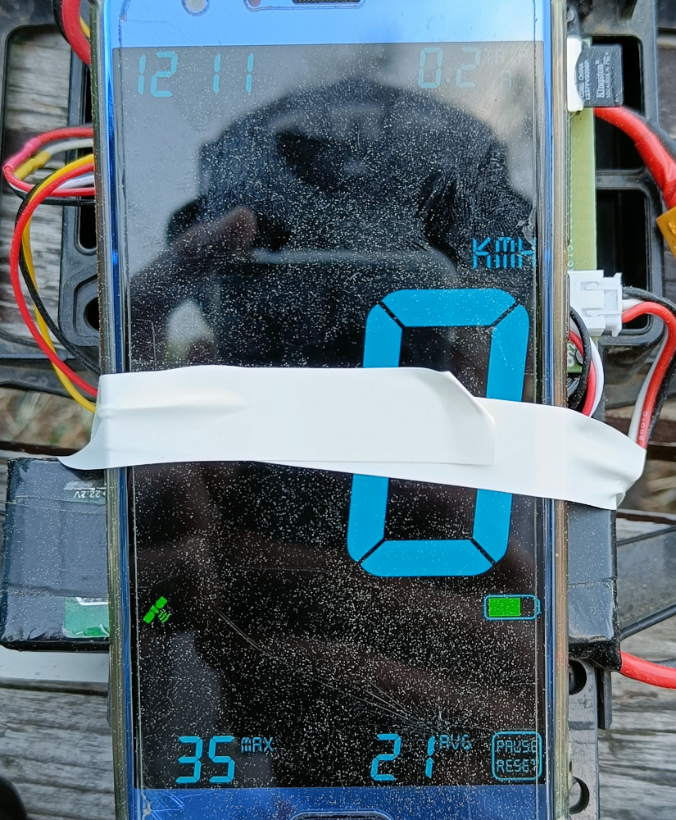
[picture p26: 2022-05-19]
Thesis/support/pic/speed_run2.jpg

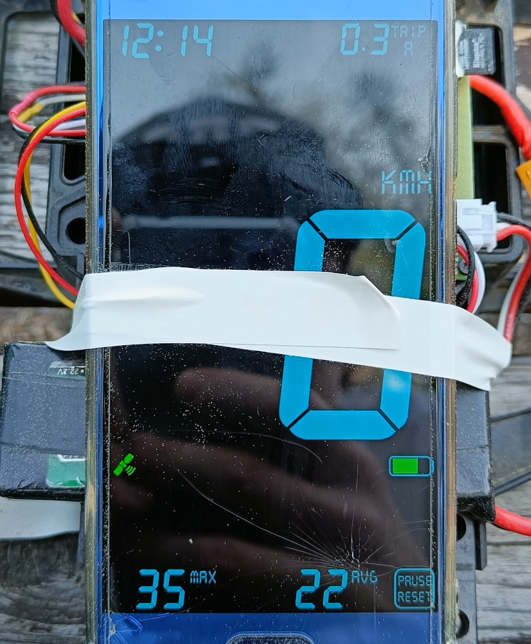
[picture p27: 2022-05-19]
Thesis/support/pic/speed_run3.jpg

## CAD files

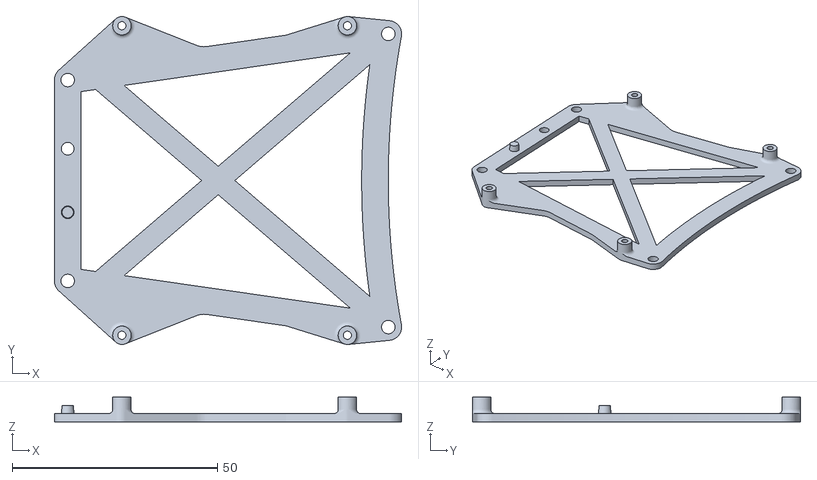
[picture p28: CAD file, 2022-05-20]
3D printed parts/frame.stl
84.7 x 80.0 x 6.00

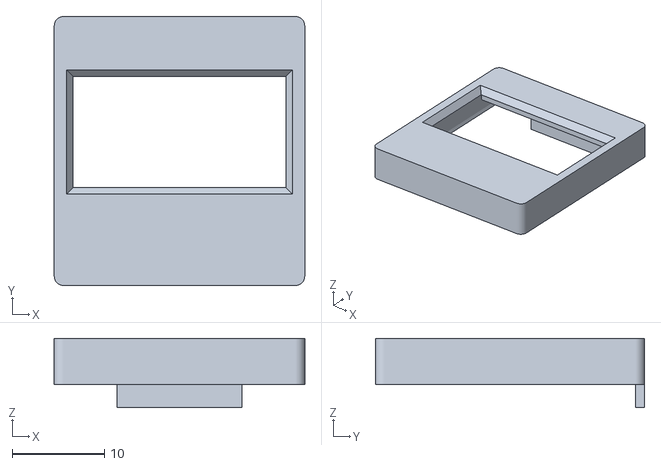
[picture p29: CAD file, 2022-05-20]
3D printed parts/oled_protection.stl
27.1 x 29.1 x 7.50

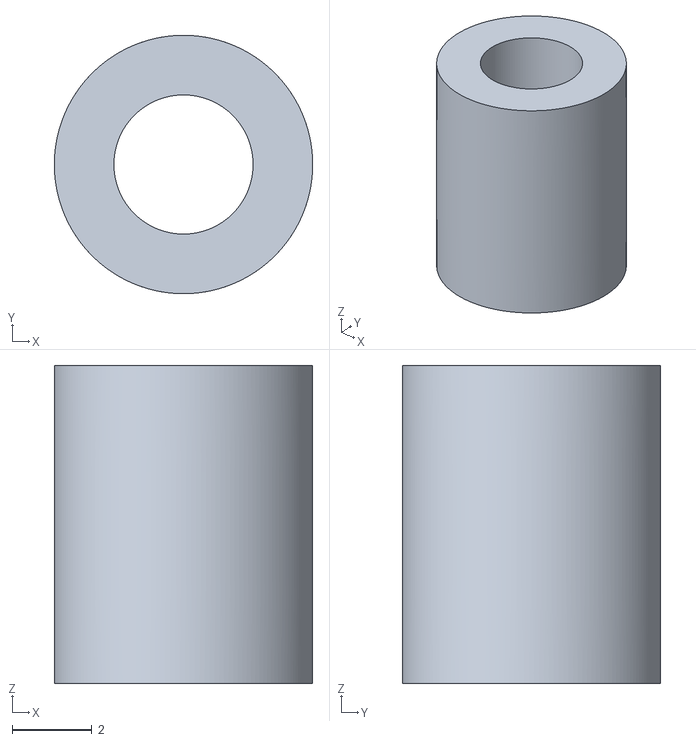
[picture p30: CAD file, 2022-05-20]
3D printed parts/dist_front.stl
6.50 x 6.50 x 8.00

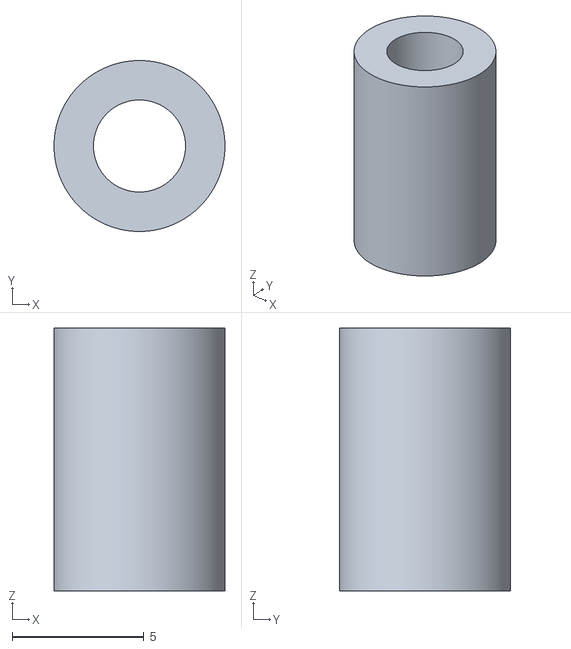
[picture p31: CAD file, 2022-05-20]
3D printed parts/dist_back.stl
6.50 x 6.50 x 10.0

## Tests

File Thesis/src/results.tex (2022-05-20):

%!TEX ROOT=main.tex

\part{Results}
\label{chap:results}
\section{Overall}
The built RC system was successfully tested in real-life conditions. The connection between the transmitter and the car is quickly established, even though the antenna is usually hidden under the plastic shell. The driving works flawlessly; the control is responsive and smooth. Trimming encoders can correct any misbehavior, for example, small steering to one side.

Suppose the signal is lost and no command arrives in \SI{250}{\ms} from the last one. In that case, the dedicated safety-timer resets actuators to their neutral position. The vehicle comes to a slow stop and waits until another command packet is successfully received.

Extra features such as OLED status display with interactive indicators also work as expected and wirelessly provide the user with additional information about the RC car.

Data logging to the SD card is operational, making it possible to record driving data and analyze them afterward. An example of the graphed output data is below in figure \ref{fig:data_graph}.
\begin{figure}[h]
\centering

\caption{Example of graphed data}
\label{fig:data_graph}
\end{figure}

The battery life was not measured as it depends on a lot of factors. However, during the testing, the car was able to drive for about an hour. The battery life of the transmitter was not estimated because the battery hardly needed to be charged.

Furthermore, two experiments were realized to obtain maximum speed and communication range.

\section{Speed}
The car's maximum speed was tested in Ladronka park on a flat asphalt cycle path. The speed was measured by GPS and consisted of three test runs. An Honor 9 smartphone running GPS speedometer app DigiHUD was taped to the chassis. Before each run, the app's statistics were reset.

The car accelerated quickly and drove in a straight line with the full throttle until it stopped accelerating visually. Then the throttle was released, and the car performed a U-turn and began accelerating again. This process was repeated at least two times in each run.

Data logging to the SD card was enabled for all three test runs to monitor battery voltage, as the motor's maximum speed depends on its supply voltage.
%Measured data from the last run are graphed in figure \ref{fig:sd_speed}. The test scheme described above is clearly visible - negative peaks in \textit{'STEER'} data paired with positive peaks in \textit{'GYRO\_Z'} data represent U-turns; saturated \textit{'THRTL'} with \textit{'VOLTAGE'} drops and \textit{'CURRENT'} peaks represent straight-line accelerations.
%\begin{figure}[h]
%\centering
%\includegraphics[width=1\linewidth]{fig/run3.pdf}
%\caption{Data from last speed-test run}
%\label{fig:sd_speed}
%\end{figure}
Although the battery voltage dropped by approximately \SI{0.1}{\V} between runs, during all three of them, the car reached a maximum speed of \SI{35}{km/h}. Photos of the results of the runs are shown in figure \ref{fig:speed}.
\begin{figure}[h]
    \centering
    \begin{subfigure}{0.32\textwidth}
    \centering
%        \includegraphics[width=1\textwidth]{fig/speed_run1.jpg}
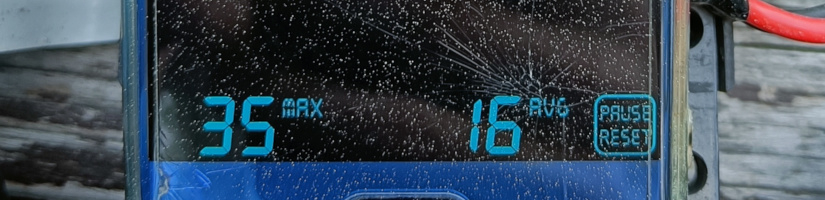
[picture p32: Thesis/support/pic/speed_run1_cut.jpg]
        
		\caption{test run 1}
    \end{subfigure}%
    \hspace{0.1cm}
    \begin{subfigure}{0.32\textwidth}
    \centering
%		\includegraphics[width=1\textwidth]{fig/speed_run2.jpg}
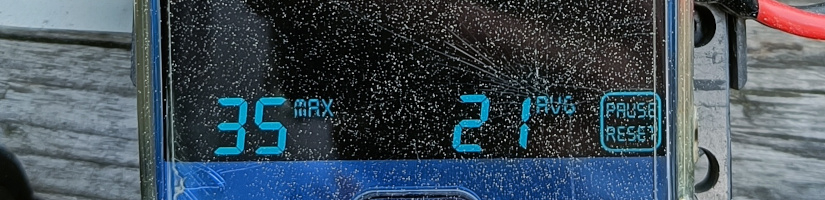
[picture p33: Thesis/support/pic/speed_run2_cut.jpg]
		
		\caption{test run 2}
    \end{subfigure}
    \hspace{0.1cm}
    \begin{subfigure}{0.32\textwidth}
    \centering
%		\includegraphics[width=1\textwidth]{fig/speed_run3.jpg}
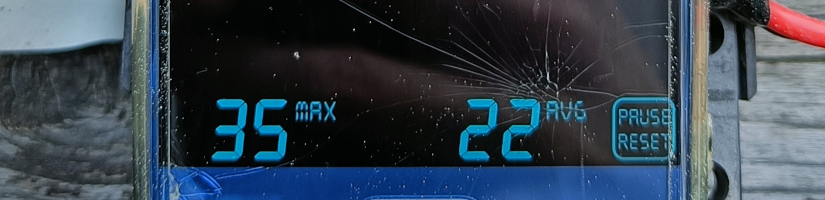
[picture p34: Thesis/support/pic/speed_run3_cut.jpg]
		
		\caption{test run 3}
    \end{subfigure}
	\caption{Results of the speed test}
    \label{fig:speed}
\end{figure}

\section{Range}
The range test was also performed in Ladronka park. The test is mainly informative since the car is~barely visible at about \SI{250}{\m}. The expected maximum range given by used communication modules was \SI{800}{\m}; therefore, the distance was calculated from GPS coordinates.

The test utilized the vehicle's signal loss detection feature. The transmitter was configured to send the steering command to keep the front wheels turned. The signal loss was easily recognizable since the signal loss detection feature resets the motor and straightens the servo. Both antennas were in a vertical position during the test for the best signal reception.

First, coordinates of the transmitter's initial position were acquired. Then the chassis was moved in a straight direction to keep the transmitter in sight until the signal began to fade.
\begin{table}[h]
   \renewcommand{\arraystretch}{1.1}
   \centering
    \caption{GPS coordinates and distances from the initial position}\label{tab:gps_dist}   
    \begin{tabular}{c c c}
       \noalign{\hrule height 1.1pt}\noalign{\smallskip}
	    & \bfseries GPS coordinates & \bfseries Calculated distance\\[0.2em]
	\noalign{\hrule height 1.1pt}\noalign{\smallskip}     
initial position		& 50.0792036N, 14.3716383E	& -- \\
occasional outages	& 50.0790850N, 14.3663733E	& \SI{375.9}{\m} \\
frequent outages		& 50.0793289N, 14.3631853E	& \SI{603.3}{\m} \\
signal 'lost'		& 50.0794572N, 14.3609497E	& \SI{763.2}{\m} \\
       \noalign{\smallskip}\noalign{\hrule height 1.1pt}
    \end{tabular}
\end{table} 

After \SI{375}{\m}, the servo started to straighten occasionally, indicating that no command packet was received within \SI{250}{\ms} from the last one. Even though the safety-timer sometimes reset the car, it was still controllable.

After \SI{603}{\m} from the initial position, the signal suffered frequent outages. The car was in a 'no signal' state more than 50\% of the time, making the control difficult.

The maximum range was measured at \SI{763}{\m}. At this distance, the signal was not completely lost. Infrequently, the command packet was successfully received, but the car remained in a 'no signal' state most of the time, making the control almost impossible.
\begin{figure}[h]
\centering
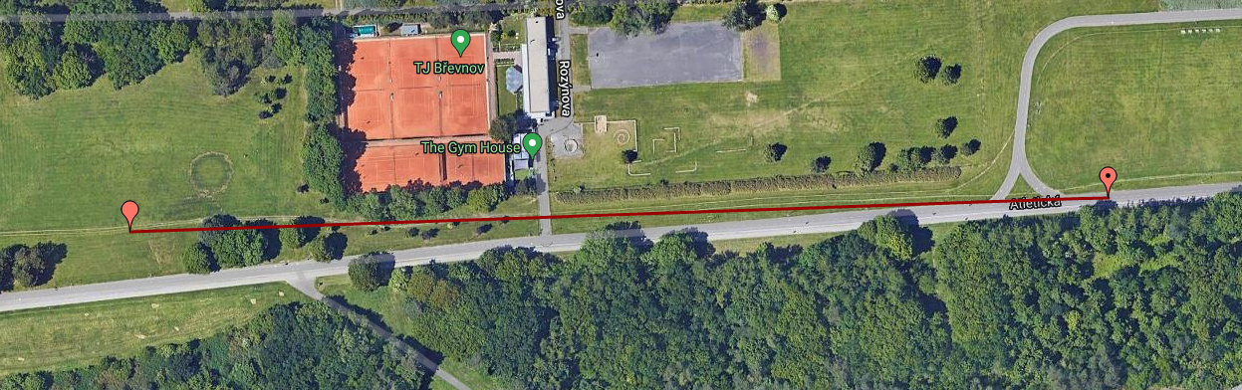
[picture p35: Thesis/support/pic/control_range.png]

\caption{Controllable distance}
\label{fig:control_range}
\end{figure}

GPS coordinates along with the calculated distance from the initial position are in table \ref{tab:gps_dist}. The measured control distance is visualized in figure \ref{fig:control_range}.

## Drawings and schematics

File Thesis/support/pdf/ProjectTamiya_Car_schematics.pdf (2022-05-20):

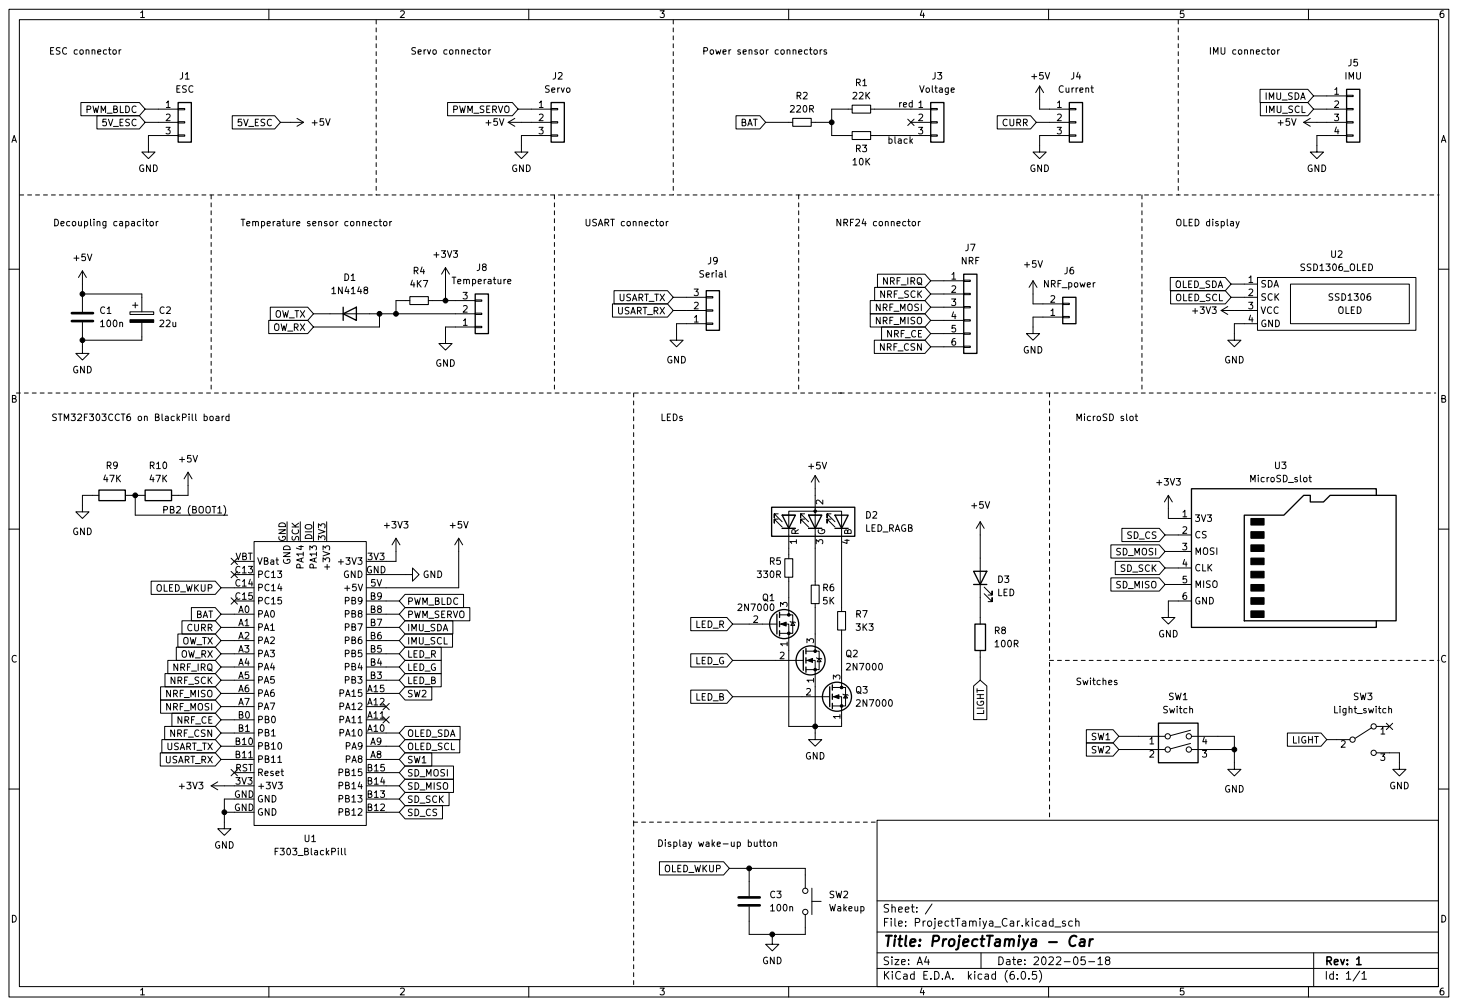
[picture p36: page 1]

IMU connector Switches Display wake-up button

GND GND GND GND

Id: 1/1 Title: ProjectTamiya - Car

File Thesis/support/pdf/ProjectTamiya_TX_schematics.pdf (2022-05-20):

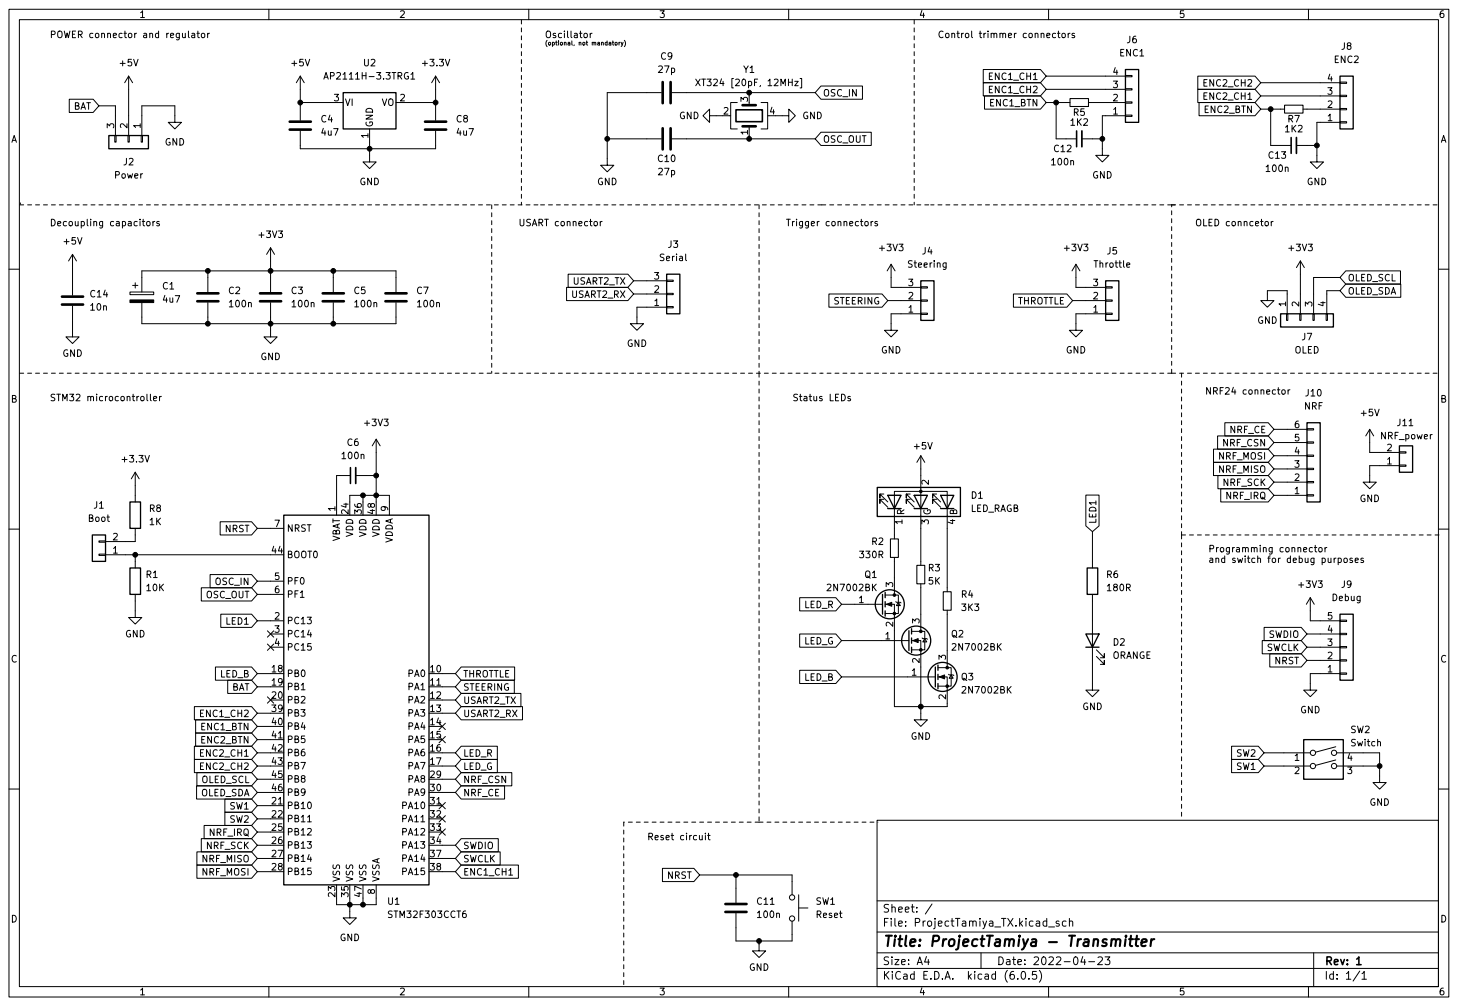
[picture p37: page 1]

POWER connector and regulator

1 PA0 10 PA1 11 PA2 12 PA3 13 PA4 14 PA5 15 PA6 16 PA7 17 PB0 18 PB1 19 PC13 2 PB2 20 PB10 21 PB11 22 VSS 23 VDD 24 PB12 25 PB13 26 PB14 27 PB15 28 PA8 29 PC14 3 PA9 30 PA10 31 PA11 32 PA12 33 PA13 34 VSS 35 VDD 36 PA14 37 PA15 38 PB3 39 PC15 4 PB4 40 PB5 41 PB6 42 PB7 43 BOOT0 44 PB8 45 PB9 46 VSS 47 VDD 48 PF0 5 PF1 6 NRST 7 VSSA

File: ProjectTamiya_TX.kicad_sch Sheet: /
Id: 1/1 Title: ProjectTamiya - Transmitter

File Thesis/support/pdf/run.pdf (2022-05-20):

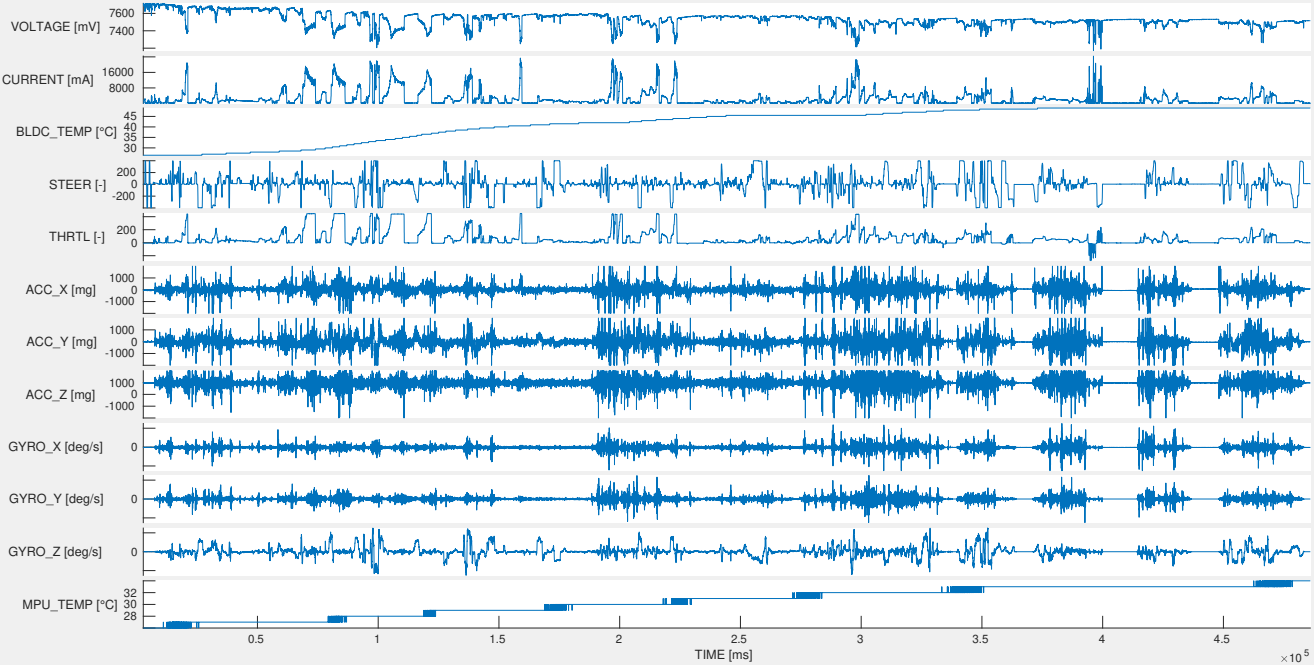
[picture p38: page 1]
VOLTAGE [mV]; 16000 CURRENT [mA]; BLDC_TEMP [°C]; STEER [-]; 200 THRTL [-]; ACC_X [mg]; ACC_Y [mg]; ACC_Z [mg]; GYRO_X [deg/s]; GYRO_Y [deg/s]; GYRO_Z [deg/s]; TIME [ms]; MPU_TEMP [°C]

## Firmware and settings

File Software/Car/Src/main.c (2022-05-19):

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
/* Includes ------------------------------------------------------------------*/
#include "main.h"
#include "fatfs.h"

/* USER CODE BEGIN Includes */
#include <stdbool.h>
#include <string.h>
#include <math.h>

#include <stdarg.h>
#include <stdio.h>

#include "project_tamiya.h"
/* USER CODE END Includes */

/* USER CODE BEGIN PD */
#define ADC_BUFF_SIZE     512

#define RES_22K           22050.0                                               // real resistor values
#define RES_10K           9710.0 
#define BAT_DIVIDER       (RES_22K + RES_10K) / RES_10K                         // constant to compute battery voltage

#define RES_47K_5V        46710.0
#define RES_47K_GND       46600.0
#define SPLY_DIVIDER      (RES_47K_5V + RES_47K_GND) / RES_47K_GND              // constant to compute supply voltage

#define VREFINT_CAL_ADDR  0x1FFFF7BA                                            // internal reference voltage calibration values address

#define SD_FORMAT         "TIME,VOLTAGE,CURRENT,BLDC_TEMP,STEER,THRTL,ACC_X,ACC_Y,ACC_Z,GYRO_X,GYRO_Y,GYRO_Z,MPU_TEMP\n"
#define SD_FORMAT_UNITS   "ms,mV,mA,deg C,-,-,mg,mg,mg,deg/s,deg/s,deg/s, deg C\n"
/* USER CODE END PD */

ADC_HandleTypeDef hadc1;
ADC_HandleTypeDef hadc2;
DMA_HandleTypeDef hdma_adc1;
DMA_HandleTypeDef hdma_adc2;

I2C_HandleTypeDef hi2c1;
I2C_HandleTypeDef hi2c2;

SPI_HandleTypeDef hspi1;
SPI_HandleTypeDef hspi2;

TIM_HandleTypeDef htim1;
TIM_HandleTypeDef htim6;
TIM_HandleTypeDef htim8;
TIM_HandleTypeDef htim15;
TIM_HandleTypeDef htim16;
TIM_HandleTypeDef htim17;

UART_HandleTypeDef huart2;
UART_HandleTypeDef huart3;
DMA_HandleTypeDef hdma_usart2_rx;
DMA_HandleTypeDef hdma_usart2_tx;

/* USER CODE BEGIN PV */
bool NRF_IRQ = false, adc_data_bat_rdy = false, adc_data_sply_rdy = false;      // flags
bool display_refresh = false, temp_received = false, temp_conv_ready = false, show_batoff = false;

bool UART_debug = true, log_data = false, unmount_sd = false;                   // flags controlled by dip switches

bool display_wakeup = false;                                                    // flag controlled by button

uint16_t STATUS_LED = LED_G_Pin;

MPU6050_t mpu;                                                                  // MPU6050 data struct

uint8_t temp_receive_buffer[9] = {0};                                           // temperature data buffer

uint16_t adc_data_bat[ADC_BUFF_SIZE*2], adc_data_sply[ADC_BUFF_SIZE*2];         // ADC data buffer

uint32_t voltage = 7500, current, vrefint, supply5, temp, temp_frac;            // values
uint16_t tx_freq = 0, tx_freq_cnt = 0;                                          // command frequency per sec
/* USER CODE END PV */

void SystemClock_Config(void);
static void MX_GPIO_Init(void);
static void MX_DMA_Init(void);
static void MX_ADC1_Init(void);
static void MX_SPI1_Init(void);
static void MX_USART2_UART_Init(void);
static void MX_I2C1_Init(void);
static void MX_SPI2_Init(void);
static void MX_I2C2_Init(void);
static void MX_TIM8_Init(void);
static void MX_USART3_UART_Init(void);
static void MX_TIM1_Init(void);
static void MX_TIM17_Init(void);
static void MX_TIM6_Init(void);
static void MX_TIM16_Init(void);
static void MX_ADC2_Init(void);
static void MX_TIM15_Init(void);
/* USER CODE BEGIN PFP */
void HAL_GPIO_EXTI_Callback(uint16_t GPIO_Pin);
void HAL_TIM_PeriodElapsedCallback(TIM_HandleTypeDef *htim);
void HAL_ADC_ConvCpltCallback(ADC_HandleTypeDef* hadc);
void HAL_UART_RxCpltCallback(UART_HandleTypeDef *huart);
void HAL_UART_TxCpltCallback(UART_HandleTypeDef *huart);

void BlinkLeds(void);
void OW_Complete(void);
void OW_Error(void);
void DS_Convert(void);
void DS_Read(uint8_t* buffer);
uint16_t DS_GetIntTemp(uint16_t temp);
void PrintError(const char *s, ...);
/* USER CODE END PFP */

/**
  * @brief  The application entry point.
  * @retval int
  */
int main(void)
{
  /* MCU Configuration--------------------------------------------------------*/

  /* Reset of all peripherals, Initializes the Flash interface and the Systick. */
  HAL_Init();

  /* Configure the system clock */
  SystemClock_Config();

  /* Initialize all configured peripherals */
  MX_GPIO_Init();
  MX_DMA_Init();
  MX_ADC1_Init();
  MX_SPI1_Init();
  MX_USART2_UART_Init();
  MX_I2C1_Init();
  MX_SPI2_Init();
  MX_I2C2_Init();
  MX_TIM8_Init();
  MX_USART3_UART_Init();
  MX_FATFS_Init();
  MX_TIM1_Init();
  MX_TIM17_Init();
  MX_TIM6_Init();
  MX_TIM16_Init();
  MX_ADC2_Init();
  MX_TIM15_Init();
  /* USER CODE BEGIN 2 */

  HAL_GPIO_WritePin(LED1_GPIO_Port, LED1_Pin, GPIO_PIN_RESET);                  // turn on LED

  ssd1306_Init();                                                               // init display
  ssd1306_DrawXBitmap(0, 0, tamiya_car_bits, tamiya_car_width, tamiya_car_height, White);
  ssd1306_UpdateScreen();

  HAL_UART_Transmit(&UART, (uint8_t*)GREETING, strlength(GREETING), UART_TIMEOUT);  // send greeting

  if(HAL_GPIO_ReadPin(SW2_GPIO_Port, SW2_Pin) == GPIO_PIN_RESET) {              // enable SD logging only if switch is ON
    UART_SendStr("Logging enabled.\n");
    if(!MPU6050_Init()) {
      PrintError("MPU init error!");
      Error_Handler();
    }
    log_data = true;
    UART_SendStr("MPU6050 initialized!\n");
  }

                                                                                // start PWMs
  HAL_TIM_PWM_Start(&htim8, SERVO_CHANNEL);                                     // servo
  HAL_TIM_PWM_Start(&htim8, BLDC_CHANNEL);                                      // bldc
  // __HAL_TIM_SET_COMPARE(&htim8, SERVO_CHANNEL, PT_SERVO_NEUTRAL);            // reset servo
  // __HAL_TIM_SET_COMPARE(&htim8, BLDC_CHANNEL, PT_MOTOR_NEUTRAL);             // reset bldc
  UART_SendStr("PWMs started!\n");

  OneWire_Init();                                                               // init 1-Wire bus and temperature sensor
  OneWire_SetCallback(OW_Complete, OW_Error);
  DS_Convert();                                                                 // request first temperature conversion (~750ms)
  
  BlinkLeds();                                                                  // blink RGB led

  if(HAL_ADCEx_Calibration_Start(&hadc1, ADC_SINGLE_ENDED) !=  HAL_OK) {        // ADC calibration
    PrintError("ADC1 calib failed!");
    Error_Handler();
  }
  if(HAL_ADCEx_Calibration_Start(&hadc2, ADC_SINGLE_ENDED) !=  HAL_OK) {
    PrintError("ADC2 calib failed!");
    Error_Handler();
  }
  UART_SendStr("Both ADCs succesfully calibrated!\n");

  uint16_t vrefint_cal = *((uint16_t*)VREFINT_CAL_ADDR);                        // get internal ref voltage calibration value

  if(!nRF24_InitModule()) {                                                     // init communication module
    PrintError("nRF24 init error!");
    Error_Handler();
  }

  FATFS FatFs;                                                                  // variables for FatFS
  FIL file;
  volatile FRESULT fres;
  static char log_buffer[128];

  if(log_data) {                                                                // prepare SD card
    UART_SendStr("Preparing SD card...\n");

    fres = f_mount(&FatFs, "", 1);                                              // 1 = mount now
    if(fres != FR_OK) {
      PrintError("f_mount error (%i)!", fres);
      Error_Handler();
    }

    DWORD free_clusters, free_sectors, total_sectors;                           // SD card statistics
    FATFS* getFreeFs;

    fres = f_getfree("", &free_clusters, &getFreeFs);
    if(fres != FR_OK) {
      PrintError("f_getfree error (%i)!", fres);
      Error_Handler();
    }

    total_sectors = (getFreeFs->n_fatent - 2) * getFreeFs->csize;               // formula comes from ChaN's FatFS documentation
    free_sectors = free_clusters * getFreeFs->csize;

    UART_SendStr("SD card stats:\n  ");
    UART_SendInt(total_sectors / 2);
    UART_SendStr(" KiB total drive space, ");
    UART_SendInt(free_sectors / 2);
    UART_SendStr(" KiB available.\n");

    
    DIR dir;                                                                    // get number of files on SD
    FILINFO fno;
    uint16_t num_files = 0;

    UART_SendStr("Opening /logs folder...\n");
    fres = f_opendir(&dir, "/logs");                                            // open logs folder
    if(fres == FR_NO_PATH) {
      fres = f_mkdir("logs");                                                   // create it if it does not exist
      if (fres != FR_OK) {
        PrintError("f_mkdir error (%i)!", fres);
        Error_Handler();
      }
    }
    
    do {                                                                        // iterate over files in folder
        f_readdir(&dir, &fno);
        if(fno.fname[0] != 0) {
          UART_SendStr("File found: ");
          UART_SendStr(fno.fname);
          UART_SendStr("\n");

          num_files++;                                                          // increment counter
        }
    } while(fno.fname[0] != 0);
    f_closedir(&dir);

    UART_SendStr("Number of files in /logs folder: ");
    UART_SendInt(num_files);
    UART_SendStr("\n");

    static char log_fname[64];                                                  // static inits to zeros
    sprintf(log_fname, "/logs/log_%03i.csv", num_files);

    fres = f_open(&file, log_fname, FA_CREATE_ALWAYS | FA_WRITE);               // try to open file
    if(fres != FR_OK) {
      PrintError("f_open error (%i)!", fres);
      Error_Handler();
    }

    fres = f_lseek(&file, 10240000);                                             // pre-allocate 10MiB of space, shoul be enough for ~40 min of logs
    if(fres != FR_OK || f_tell(&file) != 10240000) {
      PrintError("f_lseek error (%i)!", fres);
      Error_Handler();
    }

    fres = f_lseek(&file, 0);                                                   // return back to the beginning
    if(fres != FR_OK || f_tell(&file) != 0) {
      PrintError("f_lseek error (%i)!", fres);
      Error_Handler();
    }
    UART_SendStr("Pre-allocation done.\n");

    strncpy(log_buffer, SD_FORMAT, strlen(SD_FORMAT)+1);                        // start file with description of units
    UINT bytesWrote;
    fres = f_write(&file, log_buffer, strlen(log_buffer), &bytesWrote);

    strncpy(log_buffer, SD_FORMAT_UNITS, strlen(SD_FORMAT_UNITS)+1);
    fres = f_write(&file, log_buffer, strlen(log_buffer), &bytesWrote);
    if(fres == FR_OK) {
      UART_SendStr("Write to ");
      UART_SendStr(log_fname);
      UART_SendStr(" succesful.\n");
    } else {
      PrintError("f_write error (%i)!", fres);
      Error_Handler();
    }
    f_sync(&file);                                                              // sync file

    UART_SendStr("SD card ready!\n");
  }

                                                                                // start timers
  HAL_TIM_Base_Start_IT(&htim1);                                                // 50hz data
  HAL_TIM_Base_Start_IT(&htim17);                                               // safety timer (4Hz)
  HAL_TIM_Base_Start_IT(&htim16);                                               // OLED display refresh (4Hz)
  HAL_TIM_Base_Start_IT(&htim6);                                                // per-sec statistics
  HAL_TIM_Base_Start_IT(&htim15);                                               // display ON timer; to trigger the first interrupt
  UART_SendStr("Timers started.\n");

  HAL_TIM_Base_Stop_IT(&htim15);                                                // turn the timer back off and wait for button

  ssd1306_SetDisplayOn(0);                                                      // turn off display

  /* USER CODE END 2 */

  /* Infinite loop */
  /* USER CODE BEGIN WHILE */

  uint8_t status, size;                                                         // nRF24 variables
  
  uint8_t buffer[PT_nRF24_PACKET_SIZE], ack[PT_nRF24_ACK_SIZE];                 // nRF24 msg and ack bufferš
  
  int16_t throttle = 0, steer = 0;                                              // control values

  UART_SendStr("Entering main control loop...\n");

  if(HAL_GPIO_ReadPin(SW1_GPIO_Port, SW1_Pin) == GPIO_PIN_SET) {                // deinitialize UART debug if switch is OFF
    UART_SendStr("Deinitializing UART...\n");
    HAL_UART_DeInit(&UART);
    UART_debug = false;
  }

  HAL_GPIO_WritePin(LED1_GPIO_Port, LED1_Pin, GPIO_PIN_SET);                    // turn off the led as the initialization is done

  uint32_t starttime = HAL_GetTick();
  uint32_t bytes_total = 0;

  // CoreDebug->DEMCR |= CoreDebug_DEMCR_TRCENA_Msk;                            // enable cycle counter for debug purposes
  // DWT->CYCCNT = 0;
  // DWT->CTRL |= DWT_CTRL_CYCCNTENA_Msk;

  // volatile unsigned long t1 = 0, t2 = 0;
  // t1 = DWT->CYCCNT;
  // t2 = DWT->CYCCNT;

  while (1)
  {
    if(NRF_IRQ) {                                                               // nRF external interrupt
      status = nRF24_GetStatus();

      if(status & nRF24_FLAG_RX_DR) {                                           // data in RX data register
        uint8_t temp_byte = (temp & 0x7F) | (temp_frac ? (1 << 7) : (0 << 7));  // prepare ACK packet
        memmove(&ack[0], &voltage, sizeof(uint16_t));
        memmove(&ack[2], &temp_byte, sizeof(uint8_t));
        
        nRF24_ReceivePacket(buffer, &size, ack);

        if(size == PT_nRF24_PACKET_SIZE) {
          memmove(&throttle, &buffer, sizeof(int16_t));                         // parse control data
          memmove(&steer, &buffer[2], sizeof(int16_t));

          if(steer > PT_MAXSTEER) {                                             // check and clip values
            steer = PT_MAXSTEER;
          }
          else if(steer < -PT_MAXSTEER) {
            steer = -PT_MAXSTEER;
          }
          if(throttle > PT_MAXTHRTL) {
            throttle = PT_MAXTHRTL;
          }
          else if(throttle < -PT_MAXTHRTL) {
            throttle = -PT_MAXTHRTL;
          }
          
          __HAL_TIM_SET_COMPARE(&htim8, SERVO_CHANNEL, PT_SERVO_NEUTRAL - steer);  // update PWM settings
          __HAL_TIM_SET_COMPARE(&htim8, BLDC_CHANNEL, PT_MOTOR_NEUTRAL - throttle);

          __HAL_TIM_SET_COUNTER(&htim17, 0);                                    // reset safety timer

          tx_freq_cnt++;
        }
      }

      NRF_IRQ = false;                                                          // reset flag
    }


    if(temp_conv_ready) {                                                       // temperature conversion in sensor ready
      memset(temp_receive_buffer, 0, sizeof(temp_receive_buffer));
      DS_Read((uint8_t*)&temp_receive_buffer);

      if(log_data) {                                                            // also sync the file if logging is enabled
        f_sync(&file);

        if(UART_debug) {
          UART_SendStr("FILE SYNCED! ");
          UART_SendInt(bytes_total);
          UART_SendStr(" bytes total\n");
        }

        bytes_total = 0;                                                        // reset counter
      }
    }


    if(temp_received) {                                                         // temperature received   
      uint16_t temp_raw = (temp_receive_buffer[1] << 8) | temp_receive_buffer[0];
      temp = DS_GetIntTemp(temp_raw);                                           // convert integer temperature

      if((temp_raw & (0x8)) == 0x8) {                                           // check bit associated with 2^(-1) deg C
        temp_frac = 5;
      } else {
        temp_frac = 0;
      }
      
      temp_received = false;                                                    // reset flag
      DS_Convert();                                                             // start next conversion
    }


    if(adc_data_bat_rdy && adc_data_sply_rdy) {                                 // ADC conversion complete interrupt (20Hz)
      voltage = current = vrefint = supply5 = 0;                                // reset

      for(int i = 0; i < 2*ADC_BUFF_SIZE; i += 2) {                             // average values
        voltage += (uint16_t)adc_data_bat[i + 0];
        current += (uint16_t)adc_data_bat[i + 1];
        vrefint += (uint16_t)adc_data_sply[i + 0];
        supply5 += (uint16_t)adc_data_sply[i + 1];
      }
      voltage /= ADC_BUFF_SIZE;
      current /= ADC_BUFF_SIZE;
      vrefint /= ADC_BUFF_SIZE;
      supply5 /= ADC_BUFF_SIZE;

      uint16_t vdda = 3300 * vrefint_cal / vrefint;                             //calculate VDDA
      
      supply5 = supply5 * vdda / 4095 + 24;                                     // calculate supply voltage (5V)
                                                                                // 24mV is a "magic constant", it is an offset between BOOT1 and actual MCU pin
      supply5 *= SPLY_DIVIDER;
      voltage = voltage * vdda / 4095;                                          // calculate the actual battery voltage
      voltage *= BAT_DIVIDER;
      current = current * vdda / 4095;                                          // calculate current
      current = (((supply5 / 2.0) - current) * 1000 / 27.06) - 721.95;          // 66 mV/A from datasheet * 0.41 correction - 296/0.41 offset
      // current = ((supply5 / 2.0) - current) * 1000 / 66.0;                   // 66 mV/A from datasheet
      
      if(log_data) {
        MPU6050_ReadAll(&mpu);                                                  // get MPU data

        memset(log_buffer, 0, sizeof(log_buffer));                              // prepare log entry
        int num = snprintf(log_buffer, 128, "%u,%u,%u,%u.%u,%i,%i,%i,%i,%i,%i,%i,%i,%i\n",\
          HAL_GetTick() - starttime, voltage, current, temp, temp_frac, steer, throttle, (int)(mpu.Ax*1000),\
          (int)(mpu.Ay*1000), (int)(mpu.Az*1000), (int)mpu.Gx, (int)mpu.Gy, (int)mpu.Gz, (int)mpu.temp);

        UINT bytesWrote;
        fres = f_write(&file, log_buffer, num, &bytesWrote);                    // write log entry to the file
        bytes_total += bytesWrote;

        if(fres != FR_OK) {
          PrintError("f_write error (%i)\r\n");
          unmount_sd = true;                                                    // try to unmount
          if(UART_debug) {
            HAL_Delay(1000);                                                    // delay to notice the error
          }
        }
      }

      if(UART_debug) {                                                          // send data to UART
        UART_SendStr("BAT: ");
        UART_SendInt(voltage);
        UART_SendStr("mV, ");
        UART_SendInt(current);
        UART_SendStr("mA; SUPPLY: ");
        UART_SendInt(vdda);
        UART_SendStr("mV, ");
        UART_SendInt(supply5);
        UART_SendStr("mV; ");
        UART_SendStr("BLDC temp: ");
        UART_SendInt(temp);
        UART_SendStr(".");
        UART_SendInt(temp_frac);
        UART_SendStr("C\n");
      }

      adc_data_bat_rdy = adc_data_sply_rdy = false;                             // reset flags
    }


    if(log_data && unmount_sd) {
      f_truncate(&file);                                                        // truncate unused area
      f_close(&file);                                                           // close file
      UART_SendStr("File saved.\n");

      f_mount(NULL, "", 0);                                                     // unmount SD card
      UART_SendStr("SD unmounted succesfully!\n");

      log_data = unmount_sd = false;                                            // reset flags
    }


    if(display_refresh && display_wakeup) {                                     // OLED display refresh interrupt
      ssd1306_Fill(Black);                                                      // clear
      OLED_TempInfo(10, 0, temp, temp_frac, White, Font_7x10);
      OLED_BatInfo(90, 0, voltage, White, Font_7x10, show_batoff);
      OLED_SignalInfo(45, 19, tx_freq, White, Font_6x8);                        // display commands per sec
      ssd1306_UpdateScreen();

      display_refresh = false;                                                  // reset flag
    }    

    /* USER CODE END WHILE */

    /* USER CODE BEGIN 3 */
  }
  /* USER CODE END 3 */
}

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
/* USER CODE BEGIN 4 */

/* CALLBACKS */
void HAL_GPIO_EXTI_Callback(uint16_t GPIO_Pin) {
  if(GPIO_Pin == NRF_IRQ_Pin) {                                                 // nRF24 interrupt
    NRF_IRQ = true;

    HAL_GPIO_WritePin(LED_B_GPIO_Port, LED_B_Pin, GPIO_PIN_RESET);              // reset no signal led
    HAL_GPIO_TogglePin(GPIOB, STATUS_LED);
  }
  else if(GPIO_Pin == OLED_WKUP_Pin) {                                          // OLED wakeup button
    UART_SendStr("OLED_WKUP\n");

    HAL_TIM_Base_Stop_IT(&htim15);                                              // reset counter state
    __HAL_TIM_SET_COUNTER(&htim15, 0);                                          // set counter back to 0 in case the timer was active
    // TIM15->CR1 |= TIM_CR1_URS;                                               // enable only timer overflow interrupts (doesnt work, IRQ still triggered)
    HAL_TIM_Base_Start_IT(&htim15);                                             // start timer

    display_wakeup = true;
    ssd1306_SetDisplayOn(1);                                                    // turn display on
  }
  else if(GPIO_Pin == SW1_Pin) {                                                // switch 1 (UART)
    UART_SendStr("SW1\n");

    if(HAL_GPIO_ReadPin(SW1_GPIO_Port, SW1_Pin) == GPIO_PIN_RESET) {
      MX_USART3_UART_Init();
      UART_debug = true;
      UART_SendStr("UART initialized!\n");
    } else {
      UART_SendStr("Deinitializing UART...\n");
      HAL_UART_DeInit(&UART);
      UART_debug = false;
    }
  }
  else if(GPIO_Pin == SW2_Pin) {                                                // switch 2 (SD logging)
    UART_SendStr("SW2\n");
    unmount_sd = true;
  }
}
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

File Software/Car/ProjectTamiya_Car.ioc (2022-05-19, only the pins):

PB14.GPIO_Label=SD_MISO
PA6.GPIO_Label=NRF_MISO
PB6.GPIO_Label=IMU_SCL
PB13.Signal=SPI2_SCK
PB6.Signal=I2C1_SCL
PB2.Signal=ADC2_IN12
PB12.GPIO_Label=SD_CS
PB1.GPIO_Label=NRF_CSN
PA8.Signal=GPXTI8
PA0.Signal=ADC1_IN1
PB9.Signal=S_TIM8_CH3
PB1.Signal=GPIO_Output
PA10.Signal=I2C2_SDA
PA4.GPIO_Label=NRF_IRQ
PF1-OSC_OUT.Signal=RCC_OSC_OUT
PC13.Signal=GPIO_Output
PA9.GPIO_Label=OLED_SCL
PC14-OSC32_IN.Signal=GPXTI14
PB8.GPIO_Label=PWM_SERVO
PA8.GPIO_Label=SW1
PA9.Signal=I2C2_SCL
PB10.Signal=USART3_TX
PB14.Signal=SPI2_MISO
PA5.Signal=SPI1_SCK
PB4.GPIO_Label=LED_G
PB15.GPIO_Label=SD_MOSI
PA1.GPIO_Label=CURR
PA4.Signal=GPXTI4
PB5.Signal=GPIO_Output
PA5.GPIO_Label=NRF_SCK
PF0-OSC_IN.Signal=RCC_OSC_IN
PB0.Signal=GPIO_Output
Mcu.UserName=STM32F303CCTx
PA0.GPIO_Label=BAT
PB0.GPIO_Label=NRF_CE
PC13.GPIO_Label=LED1
PB13.GPIO_Label=SD_SCK
PB11.Signal=USART3_RX
PB15.Signal=SPI2_MOSI
PA15.GPIO_Label=SW2
PA10.GPIO_Label=OLED_SDA
PB7.Signal=I2C1_SDA
PB7.GPIO_Label=IMU_SDA
PA6.Signal=SPI1_MISO
PA2.GPIO_Label=OW_TX
PA15.Signal=GPXTI15
PB5.GPIO_Label=LED_R
PC14-OSC32_IN.GPIO_Label=OLED_WKUP
PB4.Signal=GPIO_Output
PA3.Signal=USART2_RX
PB3.GPIO_Label=LED_B
PB9.GPIO_Label=PWM_BLDC
PA13.Signal=SYS_JTMS-SWDIO
PA1.Signal=ADC1_IN2
PA2.Signal=USART2_TX
PB3.Signal=GPIO_Output
PA7.GPIO_Label=NRF_MOSI
PA14.Signal=SYS_JTCK-SWCLK
PB2.GPIO_Label=SPLY
PB8.Signal=S_TIM8_CH2
PB12.Signal=GPIO_Output
PA3.GPIO_Label=OW_RX
PA7.Signal=SPI1_MOSI

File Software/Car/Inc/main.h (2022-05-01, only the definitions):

#define LED1_Pin GPIO_PIN_13
#define LED1_GPIO_Port GPIOC
#define OLED_WKUP_Pin GPIO_PIN_14
#define OLED_WKUP_GPIO_Port GPIOC
#define OLED_WKUP_EXTI_IRQn EXTI15_10_IRQn
#define BAT_Pin GPIO_PIN_0
#define BAT_GPIO_Port GPIOA
#define CURR_Pin GPIO_PIN_1
#define CURR_GPIO_Port GPIOA
#define OW_TX_Pin GPIO_PIN_2
#define OW_TX_GPIO_Port GPIOA
#define OW_RX_Pin GPIO_PIN_3
#define OW_RX_GPIO_Port GPIOA
#define NRF_IRQ_Pin GPIO_PIN_4
#define NRF_IRQ_GPIO_Port GPIOA
#define NRF_IRQ_EXTI_IRQn EXTI4_IRQn
#define NRF_SCK_Pin GPIO_PIN_5
#define NRF_SCK_GPIO_Port GPIOA
#define NRF_MISO_Pin GPIO_PIN_6
#define NRF_MISO_GPIO_Port GPIOA
#define NRF_MOSI_Pin GPIO_PIN_7
#define NRF_MOSI_GPIO_Port GPIOA
#define NRF_CE_Pin GPIO_PIN_0
#define NRF_CE_GPIO_Port GPIOB
#define NRF_CSN_Pin GPIO_PIN_1
#define NRF_CSN_GPIO_Port GPIOB
#define SPLY_Pin GPIO_PIN_2
#define SPLY_GPIO_Port GPIOB
#define SD_CS_Pin GPIO_PIN_12
#define SD_CS_GPIO_Port GPIOB
#define SD_SCK_Pin GPIO_PIN_13
#define SD_SCK_GPIO_Port GPIOB
#define SD_MISO_Pin GPIO_PIN_14
#define SD_MISO_GPIO_Port GPIOB
#define SD_MOSI_Pin GPIO_PIN_15
#define SD_MOSI_GPIO_Port GPIOB
#define SW1_Pin GPIO_PIN_8
#define SW1_GPIO_Port GPIOA
#define SW1_EXTI_IRQn EXTI9_5_IRQn
#define OLED_SCL_Pin GPIO_PIN_9
#define OLED_SCL_GPIO_Port GPIOA
#define OLED_SDA_Pin GPIO_PIN_10
#define OLED_SDA_GPIO_Port GPIOA
#define SW2_Pin GPIO_PIN_15
#define SW2_GPIO_Port GPIOA
#define SW2_EXTI_IRQn EXTI15_10_IRQn
#define LED_B_Pin GPIO_PIN_3
#define LED_B_GPIO_Port GPIOB
#define LED_G_Pin GPIO_PIN_4
#define LED_G_GPIO_Port GPIOB
#define LED_R_Pin GPIO_PIN_5
#define LED_R_GPIO_Port GPIOB
#define IMU_SCL_Pin GPIO_PIN_6
#define IMU_SCL_GPIO_Port GPIOB
#define IMU_SDA_Pin GPIO_PIN_7
#define IMU_SDA_GPIO_Port GPIOB
#define PWM_SERVO_Pin GPIO_PIN_8
#define PWM_SERVO_GPIO_Port GPIOB
#define PWM_BLDC_Pin GPIO_PIN_9
#define PWM_BLDC_GPIO_Port GPIOB
#define SD_SPI_HANDLE hspi2

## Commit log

2022-02-26 STM32CubeMX configuration for Transmitter
2022-02-26 Kicad schematics for Transmitter with assigned footprints
    [ProjectTamiya_TX.kicad_pcb, ProjectTamiya_TX.kicad_sch]
2022-02-26 Better folder naming
    [ProjectTamiya_TX.kicad_pcb, ProjectTamiya_TX.kicad_sch]
2022-03-06 Small schematics adjustments
    [ProjectTamiya_TX.kicad_sch]
2022-03-06 PCB draft
    [ProjectTamiya_TX.kicad_pcb]
2022-03-06 Switch pin assignment change, updated schematics, complete PCB
    [ProjectTamiya_TX.kicad_pcb, ProjectTamiya_TX.kicad_sch]
2022-03-12 Rerouted tracks to have bigger spaces and other adjustments
    [ProjectTamiya_TX.kicad_pcb]
2022-03-13 Routing adjustments, curved tracks
    [ProjectTamiya_TX.kicad_pcb]
2022-03-13 Copper area correction
    [ProjectTamiya_TX.kicad_pcb]
2022-03-18 Small PCB routing changes, silkscreen improvements
    [ProjectTamiya_TX.kicad_pcb, ProjectTamiya_TX.kicad_sch]
2022-03-27 Final checkup and small adjustments
    [ProjectTamiya_TX.kicad_pcb, ProjectTamiya_TX.kicad_sch]
2022-03-27 Added gerber files for JLCPCB
    [ProjectTamiya_TX-B_Cu.gbl, ProjectTamiya_TX-B_Mask.gbs, ProjectTamiya_TX-B_Silkscreen.gbo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]
2022-03-27 Regenerated gerbers to be sure they are up-to-date with the schematic
    [ProjectTamiya_TX-B_Cu.gbl, ProjectTamiya_TX-B_Mask.gbs, ProjectTamiya_TX-B_Silkscreen.gbo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]
2022-03-30 Removed some of the ground vias
    [ProjectTamiya_TX.kicad_pcb]
2022-03-30 New gerber files
    [ProjectTamiya_TX-B_Cu.gbl, ProjectTamiya_TX-B_Mask.gbs, ProjectTamiya_TX-B_Silkscreen.gbo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]
2022-04-05 Minor schematic corrections
    [ProjectTamiya_TX.kicad_sch]
2022-04-05 STM32CubeMX configuration for Car
2022-04-05 Added Kicad schematics for the Car with assigned footprints that corresponds with hand soldering
    [ProjectTamiya_Car.kicad_pcb, ProjectTamiya_Car.kicad_sch]
2022-04-12 Slight pin assignment change
2022-04-12 Wrong SPI pin naming
    [ProjectTamiya_Car.kicad_sch]
2022-04-19 Updated pin assignments
2022-04-19 Changed OLED_WKUP pin from PC15 to PC14, as only one external interrupt can be on pin 15
    [ProjectTamiya_Car.kicad_sch]
2022-04-22 Added voltage divider on PB2 to measure 5V supply
    [ProjectTamiya_Car.kicad_sch]
2022-04-22 Implemented temperature measurements
2022-04-23 Updated low voltage behaviour
2022-04-23 Corrected labels to reflect real hardware (DIP switch)
    [ProjectTamiya_TX.kicad_pcb, ProjectTamiya_TX.kicad_sch]
2022-05-01 Implemented SD card logging, smaller ACK packet size, better error handling and formating...
    [ProjectTamiya_Car.ioc, main.c, main.h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]
2022-05-01 Trigger ADC double buffer, better UART prints, formating
2022-05-02 Clock source changed to PLL with gyro_X reference
2022-05-02 Removed unused timer inicialization
2022-05-02 no_signal flag is now correctly cleared
    [main.c]
2022-05-04 OLED is now switched on by button for 5 seconds
2022-05-06 Switched to different template, added more text
2022-05-08 Finished HW section, started writing Realization section
    [voltage_divider.kicad_pcb, voltage_divider.kicad_sch]
2022-05-08 Another part of realization
    [oscillator.kicad_pcb, oscillator.kicad_sch]
2022-05-08 Car control board description
2022-05-09 No signal state will not initialize the ESC now
2022-05-09 I2C Fast Mode Plus for OLED
2022-05-16 Current sensor calibration
2022-05-18 Finally got the calibration right
2022-05-18 Added capacitor for servo decoupling
    [ProjectTamiya_Car.kicad_sch]
2022-05-19 Updates and new servo calibration
2022-05-20 Schematics correction for export
    [ProjectTamiya_Car.kicad_sch, ProjectTamiya_TX.kicad_sch]
2022-05-20 Added 3D printed parts and example logs
    [LOG_010.CSV, LOG_011.CSV, dist_back.stl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]

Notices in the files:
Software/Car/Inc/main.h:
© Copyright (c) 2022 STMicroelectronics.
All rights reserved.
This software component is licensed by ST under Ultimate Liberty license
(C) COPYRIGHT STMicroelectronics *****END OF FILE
